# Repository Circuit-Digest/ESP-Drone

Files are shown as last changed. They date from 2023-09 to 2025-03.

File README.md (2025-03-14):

# ESP-Drone

image_tooltip
<br>

<br>

For a full tutorial check out our [ESP32 Drone Article](https://circuitdigest.com/microcontroller-projects/DIY-wifi-controlled-drone).
For working video:  [How to build an ESP32 Drone](https://youtu.be/uzZjk0TQKtU).

Drones have rapidly evolved from niche hobbies to versatile tools with a wide range of applications, from photography to agriculture or even for defense and military purposes. Depending on the application, features and payload capacity their price will vary from pocket changes to a few million. Even though the basic principle behind these drones may appear simple, there is a lot of technology and computation that goes behind it for proper operations and a desired result from these drones. For example, maintaining stability while in the air requires precision sensors such as a Gyroscope and proper processing of reading taken with it. In this project we are going to make such a drone which can be easily controlled using our phones.
This DIY drone is small in size and can be built using easily available components such as ESP32 modules, MPU6050 IMU, coreless motors and plastic propellers.

<br>**For anyone who is trying to flash the firmware using ESP32 Flash Download Tool, here are the file offsets for each binary**
<br>**0x1000 bootloader.bin**
<br>**0x8000 partition-table.bin**
<br>**0x10000 ESPDrone.bin**
<br>
[Note: As this projects are very simple we are only providing the code, schemaitic, and a few essential images if you want to get the images or code explanations do check out the Circuit Digest website.
<br>
<br>

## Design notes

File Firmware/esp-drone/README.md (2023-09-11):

## ESP-Drone

* [中文](./README_cn.md)

### Introduction

**ESP-Drone** is an open source solution based on Espressif ESP32/ESP32-S2/ESP32-S3 Wi-Fi chip, which can be controlled by a mobile APP or gamepad over **Wi-Fi** connection. ESP-Drone comes with **simple hardware**, **clear and extensible code architecture**, and therefore this project can be used in **STEAM education** and other fields. The main code is ported from **Crazyflie** open source project with **GPL3.0** protocol.

> Currently support ESP32、ESP32S2、ESP32S3, please using ESP-IDF [release/v4.4](https://docs.espressif.com/projects/esp-idf/en/release-v4.4/esp32s2/get-started/index.html) branch as your develop environment

ESP-Drone

For more information, please check the sections below:
* **Getting Started**: [Getting Started](https://docs.espressif.com/projects/espressif-esp-drone/zh_CN/latest/gettingstarted.html)
* **Hardware Schematic**：[Hardware](https://docs.espressif.com/projects/espressif-esp-drone/zh_CN/latest/_static/ESP32_S2_Drone_V1_2/SCH_Mainboard_ESP32_S2_Drone_V1_2.pdf)
* **iOS APP Source code**: [ESP-Drone-iOS](https://github.com/EspressifApps/ESP-Drone-iOS)
* **Android APP Source code**: [ESP-Drone-Android](https://github.com/EspressifApps/ESP-Drone-Android)

### Features

1. Stabilize Mode
2. Height-hold Mode
3. Position-hold Mode
4. APP Control
5. CFclient Supported

Note: to implement Height-hold/Position-hold mode, extension boards are needed. For more information, see Hardware Reference. 

### Third Party Copyrighted Code

Additional third party copyrighted code is included under the following licenses.

| Component | License | Origin |Commit ID |
| :---:  | :---: | :---: |:---: |
| core/crazyflie | GPL3.0  |[Crazyflie](https://github.com/bitcraze/crazyflie-firmware) |tag_2021_01 b448553|
| lib/dsp_lib |  | [esp32-lin](https://github.com/whyengineer/esp32-lin/tree/master/components/dsp_lib) |6fa39f4c|

### Support Policy

From December 2022, we will offer limited support on this project, but Pull Request is still welcomed!

### THANKS

1. Thanks to Bitcraze for the great [Crazyflie project](https://www.bitcraze.io/%20).
2. Thanks to Espressif for the powerful [ESP-IDF framework](https://docs.espressif.com/projects/esp-idf/en/latest/esp32s2/get-started/index.html).
3. Thanks to WhyEngineer for the useful [ESP-DSP lib](https://github.com/whyengineer/esp32-lin/tree/master/components/dsp_lib).

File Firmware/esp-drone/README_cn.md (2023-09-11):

## ESP-Drone

* [English Version](./README.md)

### 简介

ESP-Drone 是基于乐鑫 ESP32/ESP32-S2/ESP32-S3 开发的小型无人机解决方案，可使用手机 APP 或游戏手柄通过 Wi-Fi 网络进行连接和控制。目前已支持自稳定飞行、定高飞行、定点飞行等多种模式。该方案硬件结构简单，代码架构清晰完善，方便功能扩展，可用于 STEAM 教育等领域。控制系统代码来自 Crazyflie 开源工程，使用 GPL3.0 开源协议。

> 目前已支持 ESP32、ESP32S2、ESP32S3, 请使用 ESP-IDF [release/v4.4](https://docs.espressif.com/projects/esp-idf/en/release-v4.4/esp32s2/get-started/index.html) 分支

ESP-Drone

* **从这里开始**: [Getting Started](https://docs.espressif.com/projects/espressif-esp-drone/zh_CN/latest/gettingstarted.html)
* **硬件原理图**：[Hardware](https://docs.espressif.com/projects/espressif-esp-drone/zh_CN/latest/_static/ESP32_S2_Drone_V1_2/SCH_Mainboard_ESP32_S2_Drone_V1_2.pdf)
* **iOS APP 源代码**: [ESP-Drone-iOS](https://github.com/EspressifApps/ESP-Drone-iOS)
* **Android APP 源代码**: [ESP-Drone-Android](https://github.com/EspressifApps/ESP-Drone-Android)

### 功能

1. 自稳定模式
2. 定高模式
3. 定点模式
4. APP 控制
5. 适配 cfclient 上位机 

注意，定高模式及定点模式需外接扩展板，详情见硬件参考。

### 支持政策

自 2022 年 12 月起，我们仅提供有限的支持，但是 Pull Request 仍然是被欢迎的！

### 第三方代码

第三方代码及证书如下：

| 组件 | License | 源代码 |Commit ID |
| :---:  | :---: | :---: |:---: |
| core/crazyflie | GPL-3.0 |[Crazyflie](https://github.com/bitcraze/crazyflie-firmware) |tag_2021_01 b448553|
| lib/dsp_lib |  | [esp32-lin](https://github.com/whyengineer/esp32-lin/tree/master/components/dsp_lib) |6fa39f4c|

### 致谢

1. 感谢 Bitcraze 开源组织提供很棒的 [Crazyflie](https://www.bitcraze.io/%20) 无人机项目代码；
2. 感谢乐鑫提供 ESP32 和 [ESP-IDF 操作系统](https://docs.espressif.com/projects/esp-idf/en/latest/esp32s2/get-started/index.html)；
3. 感谢 WhyEngineer 提供的 stm32 dsp 移植库 [esp-dsp](https://github.com/whyengineer/esp32-lin/tree/master/components/dsp_lib)。

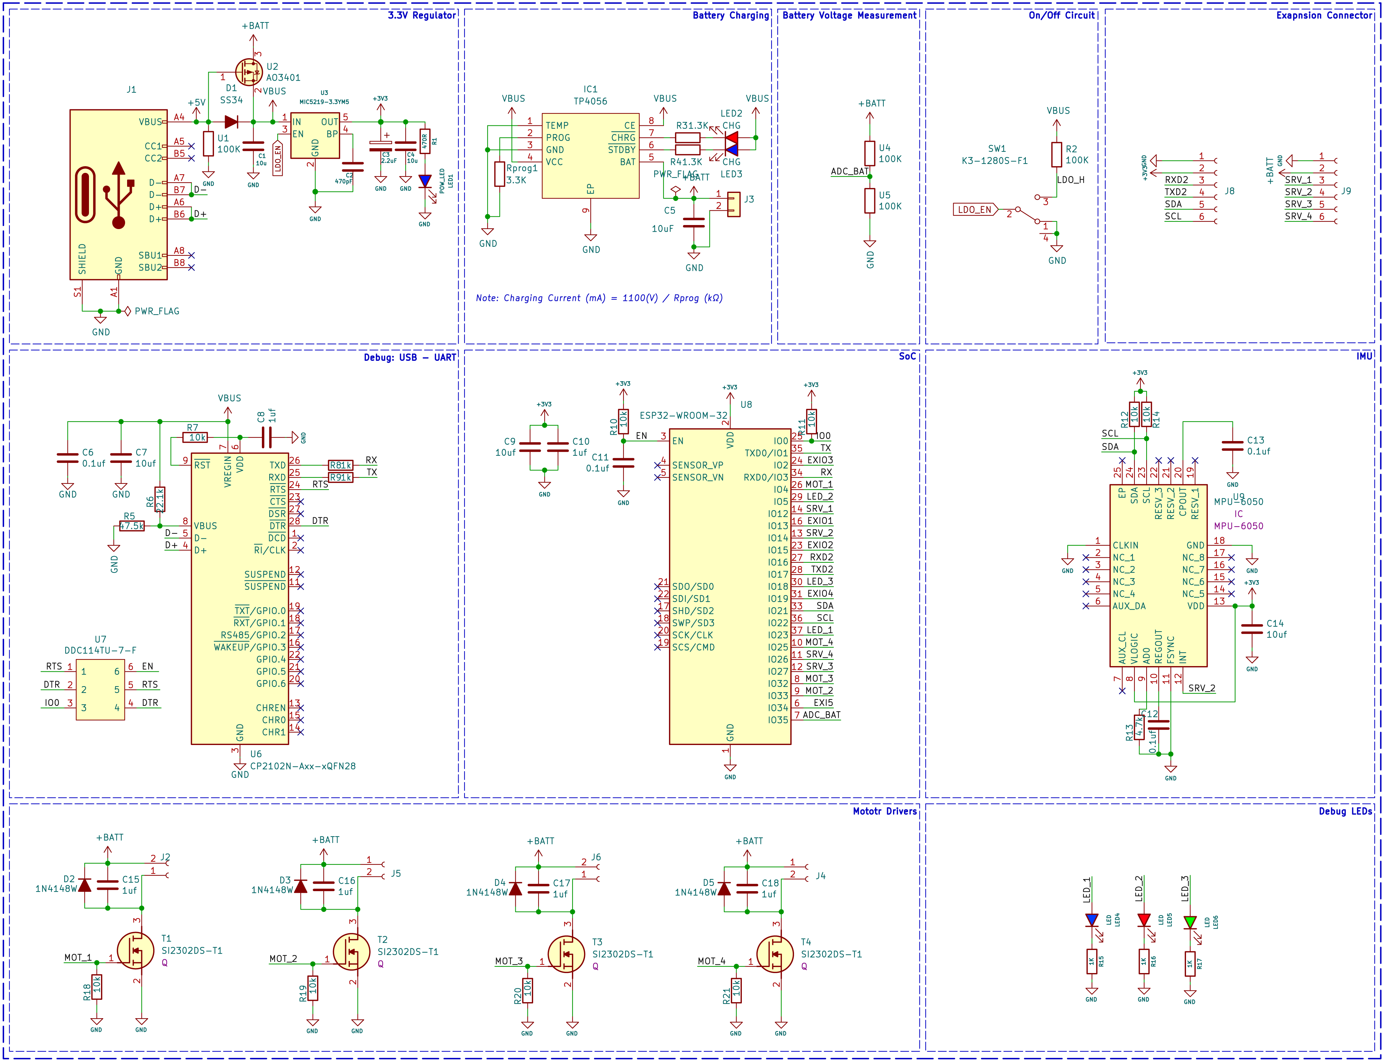
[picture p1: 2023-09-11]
ESP32 drone Schematics.png

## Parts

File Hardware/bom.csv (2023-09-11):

Designator | Footprint | Quantity | Value | LCSC Part #
C1, C4 | 603 | 2 | 10u
C10, C15, C16, C17, C18, C8 | 603 | 6 | 1uf
C11, C12, C13, C6 | 603 | 4 | 0.1uf
C14, C5, C7, C9 | 603 | 4 | 10uf
C2 | 603 | 1 | 470pF
C3 | 805 | 1 | 2.2uF
D1 | D_SMA | 1 | SS34
D2, D3, D4, D5 | D_SOD-323 | 4 | 1N4148W
IC1 | SOIC127P600X175-9N | 1 | TP4056
J1 | USB_C_Receptacle_HRO_TYPE-C-31-M-12 | 1 | USB_C_Receptacle_USB2.0
J2, J4, J5, J6 | JST_GH_SM02B-GHS-TB_1x02-1MP_P1.25mm_Horizontal | 4 | Conn_01x02_Female
J3 | JST_PH_B2B-PH-SM4-TB_1x02-1MP_P2.00mm_Vertical | 1 | B2B-PH-SM4-TB(LF)(SN)
J8, J9 | PinHeader_1x06_P2.54mm_Vertical | 2 | Conn_01x06_Female
LED1 | 603 | 1 | POW_LED
LED2, LED3 | 603 | 2 | CHG
LED4, LED5, LED6 | 603 | 3 | LED
R1 | 603 | 1 | 470R
R10, R11, R12, R14, R18, R19, R20, R21, R7 | 603 | 9 | 10k
R13 | 603 | 1 | 4.7k
R15, R16, R17, R8, R9 | 603 | 5 | 1K
R2, U1, U4, U5 | 603 | 4 | 100K
R3, R4 | 603 | 2 | 1.3K
R5 | 603 | 1 | 47.5k
R6 | 603 | 1 | 22.1k
Rprog1 | 603 | 1 | 3.3K
SW1 | slide switch spdt | 1 | K3-1280S-F1
T1, T2, T3, T4 | SOT95P237X112-3N | 4 | SI2302DS-T1
U2 | SOT-23 | 1 | AO3401
U3 | SOT-23-5 | 1 | MIC5219-3.3YM5
U6 | QFN-28-1EP_5x5mm_P0.5mm_EP3.35x3.35mm | 1 | CP2102N-Axx-xQFN28
U7 | SOT-363_SC-70-6 | 1 | 2N7002D
U8 | ESP32-WROOM-32 | 1 | ESP32-WROOM-32
U9 | MPU6050 | 1 | MPU-6050

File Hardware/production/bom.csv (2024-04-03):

Designator | Footprint | Quantity | Value | LCSC Part #
C1, C4 | 0603 | 2 | 10u
C10, C15, C16, C17, C18, C8 | 0603 | 6 | 1uf
C11, C12, C13, C6 | 0603 | 4 | 0.1uf
C14, C5, C7, C9 | 0603 | 4 | 10uf
C2 | 0603 | 1 | 470pF
C3 | 0805 | 1 | 2.2uF
D1 | D_SMA | 1 | SS34
D2, D3, D4, D5 | D_SOD-323 | 4 | 1N4148W
IC1 | SOIC127P600X175-9N | 1 | TP4056
J1 | USB_C_Receptacle_HRO_TYPE-C-31-M-12 | 1 | USB_C_Receptacle_USB2.0
J2, J4, J5, J6 | JST_GH_SM02B-GHS-TB_1x02-1MP_P1.25mm_Horizontal | 4 | Conn_01x02_Female
J3 | JST_PH_B2B-PH-SM4-TB_1x02-1MP_P2.00mm_Vertical | 1 | B2B-PH-SM4-TB(LF)(SN)
J8, J9 | PinHeader_1x06_P2.54mm_Vertical | 2 | Conn_01x06_Female
LED1 | 0603 | 1 | POW_LED
LED2, LED3 | 0603 | 2 | CHG
LED4, LED5, LED6 | 0603 | 3 | LED
R1 | 0603 | 1 | 470R
R10, R11, R12, R14, R18, R19, R20, R21, R7 | 0603 | 9 | 10k
R13 | 0603 | 1 | 4.7k
R15, R16, R17, R8, R9 | 0603 | 5 | 1K
R2, U1, U4, U5 | 0603 | 4 | 100K
R3, R4 | 0603 | 2 | 1.3K
R5 | 0603 | 1 | 47.5k
R6 | 0603 | 1 | 22.1k
Rprog1 | 0603 | 1 | 3.3K
SW1 | slide switch spdt | 1 | K3-1280S-F1
T1, T2, T3, T4 | SOT95P237X112-3N | 4 | SI2302DS-T1
U2 | SOT-23 | 1 | AO3401
U3 | SOT-23-5 | 1 | MIC5219-3.3YM5
U6 | QFN-28-1EP_5x5mm_P0.5mm_EP3.35x3.35mm | 1 | CP2102N-Axx-xQFN28
U7 | SOT-363_SC-70-6 | 1 | 2N7002DW
U8 | ESP32-WROOM-32 | 1 | ESP32-WROOM-32
U9 | MPU6050 | 1 | MPU-6050

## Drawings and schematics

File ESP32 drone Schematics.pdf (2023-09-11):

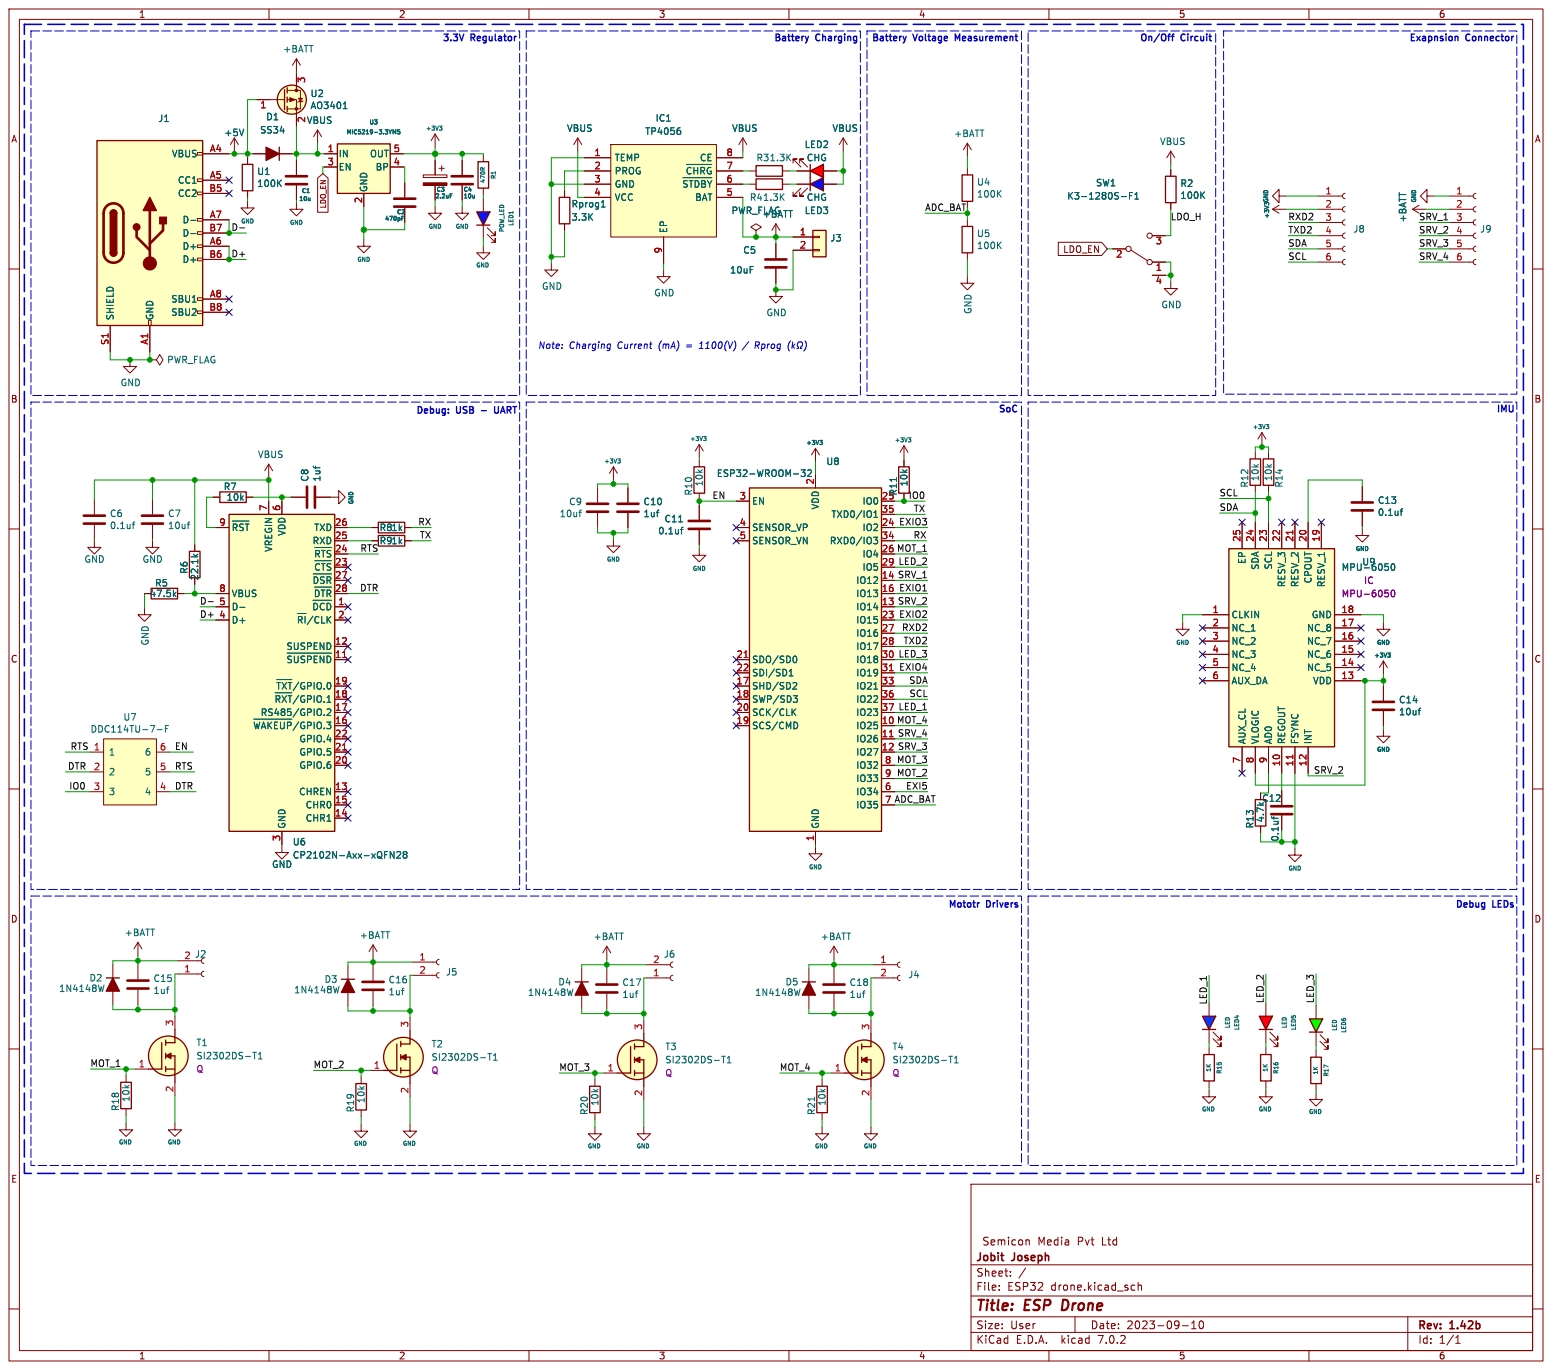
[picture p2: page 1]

IMU On/Off Circuit C8 1uf R7

Battery Voltage Measurement Note: Charging Current (mA) = 1100(V) / Rprog þÿ(k©) 3.3V Regulator

2 EN 3 BP 4 OUT 5 VBUS VBUS Rprog1

3.3K U6 CP2102N-Axx-xQFN28 ~{DCD}1 ~{SUSPEND}11 SUSPEND 12 CHREN 13 CHR1 14 CHR0 15 ~{WAKEUP}/GPIO.3

2 GPIO.6 20 GPIO.5 21 GPIO.4 22 ~{CTS} 23 ~{RTS} 24 RXD 25 TXD 26 ~{DSR} 27 ~{DTR} 28 GND

7 VBUS 8 ~{RST} 9 GND GND

~{DCD}1 ~{SUSPEND}11 SUSPEND 12 CHREN 13 CHR1 14 CHR0 15 ~{WAKEUP}/GPIO.3

2 SCK/CLK 20 SDO/SD0 21 SDI/SD1 22

Id: 1/1 Title: ESP Drone

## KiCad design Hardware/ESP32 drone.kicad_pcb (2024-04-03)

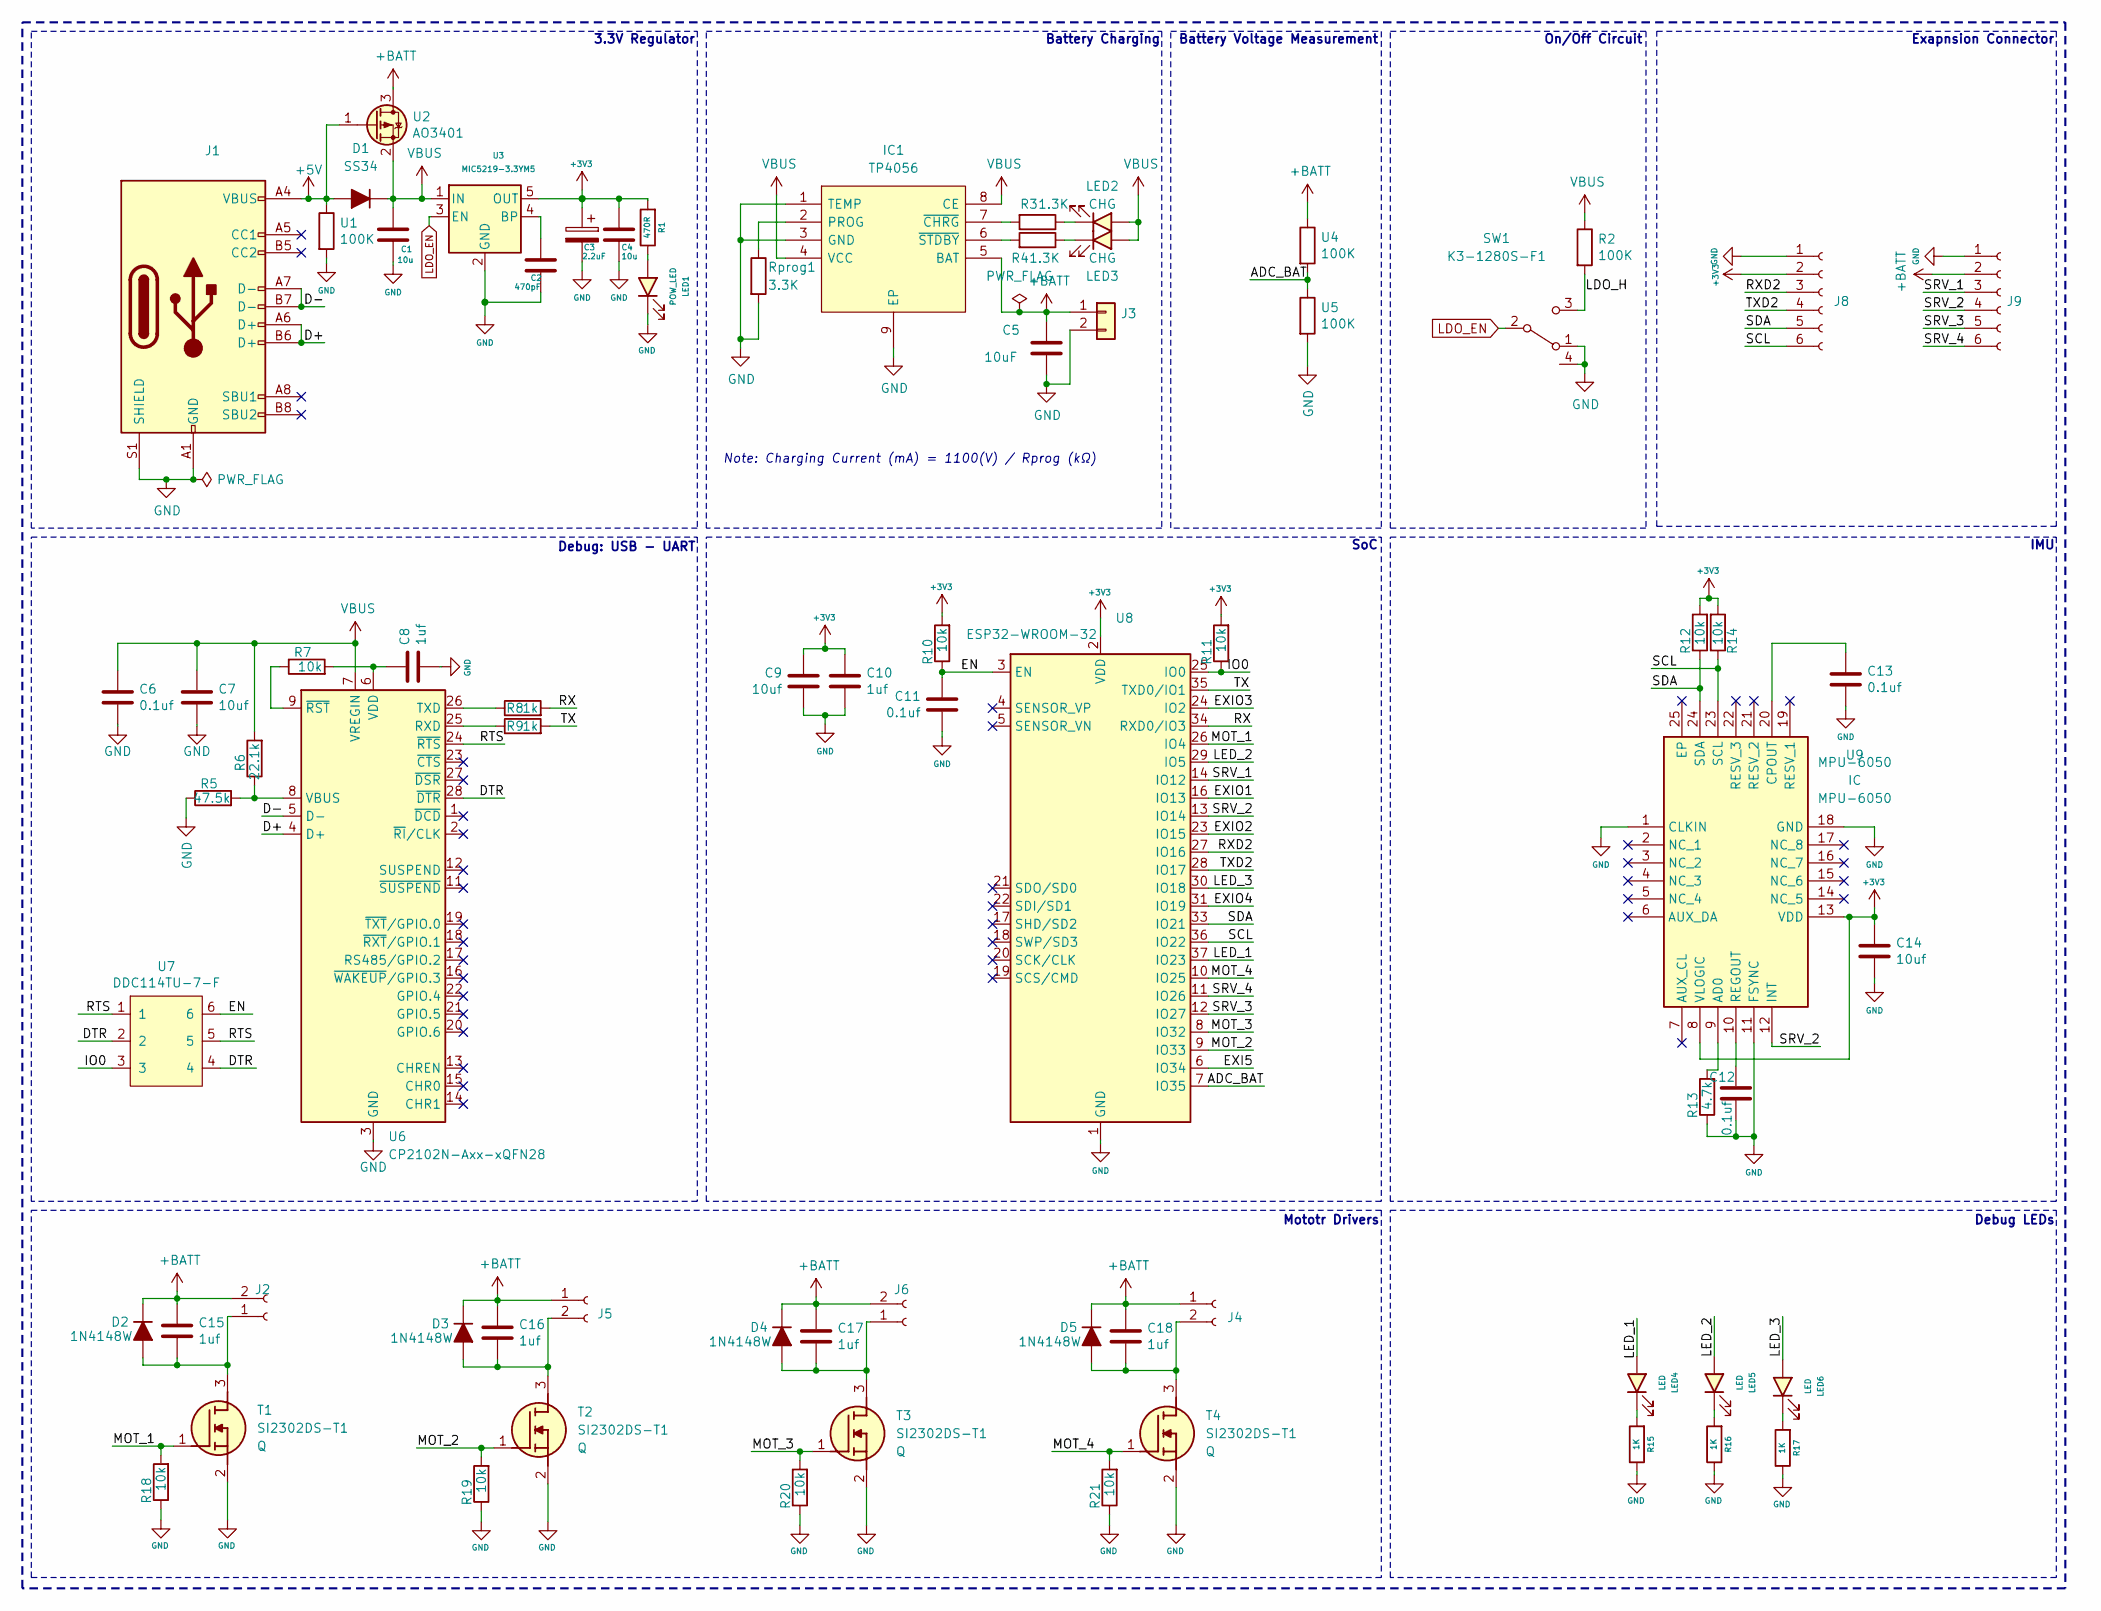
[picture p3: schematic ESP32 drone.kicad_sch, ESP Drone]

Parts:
C1, C4: 10u; C_0603_1608Metric
C2: 470pF; C_0603_1608Metric
C3: 2.2uF; C_0805_2012Metric
C5: 10uF; C_0603_1608Metric
C6, C11, C12, C13: 0.1uf; C_0603_1608Metric
C7, C9, C14: 10uf; C_0603_1608Metric
C8, C10, C15, C16, C17, C18: 1uf; C_0603_1608Metric
D1: SS34; D_SMA
D2, D3, D4, D5: 1N4148W; D_SOD-323
IC1: TP4056; SOIC127P600X175-9N; Manufacturer_Part_Number TP4056-42-ESOP8
J1: USB_C_Receptacle_USB2.0; USB_C_Receptacle_HRO_TYPE-C-31-M-12
J2, J4, J5, J6: Conn_01x02_Female; JST_GH_SM02B-GHS-TB_1x02-1MP_P1.25mm_Horizontal
J3: B2B-PH-SM4-TB(LF)(SN); JST_PH_B2B-PH-SM4-TB_1x02-1MP_P2.00mm_Vertical
J8, J9: Conn_01x06_Female; PinHeader_1x06_P2.54mm_Vertical
LED1: POW_LED; LED_0603_1608Metric
LED2, LED3: CHG; LED_0603_1608Metric
LED4, LED5, LED6: LED; LED_0603_1608Metric
R1: 470R; R_0603_1608Metric
R2: 100K; R_0603_1608Metric
R3, R4: 1.3K; R_0603_1608Metric
R5: 47.5k; R_0603_1608Metric
R6: 22.1k; R_0603_1608Metric
R7, R10, R11, R12, R14, R18, R19, R20, R21: 10k; R_0603_1608Metric
R8, R9: 1k; R_0603_1608Metric
R13: 4.7k; R_0603_1608Metric
R15, R16, R17: 1K; R_0603_1608Metric
Rprog1: 3.3K; R_0603_1608Metric
SW1: K3-1280S-F1; slide switch spdt
T1, T2, T3, T4: SI2302DS-T1; SOT95P237X112-3N; Mouser Part Number 781-SI2302DS
U1, U4, U5: 100K; R_0603_1608Metric
U2: AO3401; SOT-23
U3: MIC5219-3.3YM5; SOT-23-5
U6: CP2102N-Axx-xQFN28; QFN-28-1EP_5x5mm_P0.5mm_EP3.35x3.35mm
U7: DDC114TU-7-F; SOT-363_SC-70-6
U8: ESP32-WROOM-32
U9: MPU-6050; MPU6050; Mouser Part Number 410-MPU-6050

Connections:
+3V3: C3.1, C4.1, C9.1, C10.1, C14.1, J8.2, R1.2, R10.2, R11.2, R12.2, R14.2, U3.5 (OUT), U8.2 (VDD), U9.8 (VLOGIC), U9.13 (VDD)
+5V: D1.2 (A), J1.A4 (VBUS), J1.A9 (VBUS), J1.B4 (VBUS), J1.B9 (VBUS), U1.1, U2.1 (G)
+BATT: C5.1, C15.1, C16.1, C17.1, C18.1, D2.1 (K), D3.1 (K), D4.1 (K), D5.1 (K), IC1.5 (BAT), J2.2, J3.1, J4.1, J5.1, J6.2, J9.2, U2.3 (D), U4.1
/ADC_BAT: U4.2, U5.1, U8.7 (IO35)
/D+: J1.A6 (D+), J1.B6 (D+), U6.4 (D+)
/D-: J1.A7 (D-), J1.B7 (D-), U6.5 (D-)
/DTR: U6.28 (~DTR), U7.2, U7.4
/EN: C11.1, R10.1, U7.6, U8.3 (EN)
/EXI5: U8.6 (IO34)
/EXIO1: U8.16 (IO13)
/EXIO2: U8.23 (IO15)
/EXIO3: U8.24 (IO2)
/EXIO4: U8.31 (IO19)
/IO0: R11.1, U7.3, U8.25 (IO0)
/LDO_H: R2.2, SW1.3 (C)
/LED_1: LED4.2 (A), U8.37 (IO23)
/LED_2: LED5.2 (A), U8.29 (IO5)
/LED_3: LED6.2 (A), U8.30 (IO18)
/MOT_1: R18.2, T1.1 (G), U8.26 (IO4)
/MOT_2: R19.2, T2.1 (G), U8.9 (IO33)
/MOT_3: R20.2, T3.1 (G), U8.8 (IO32)
/MOT_4: R21.2, T4.1 (G), U8.10 (IO25)
/RTS: U6.24 (~RTS), U7.1, U7.5
/RX: R8.2, U8.34 (RXD0/IO3)
/RXD2: J8.3, U8.27 (IO16)
/SCL: J8.6, R14.1, U8.36 (IO22), U9.23 (SCL)
/SDA: J8.5, R12.1, U8.33 (IO21), U9.24 (SDA)
/SRV_1: J9.3, U8.14 (IO12)
/SRV_2: J9.4, U8.13 (IO14), U9.12 (INT)
/SRV_3: J9.5, U8.12 (IO27)
/SRV_4: J9.6, U8.11 (IO26)
/TX: R9.2, U8.35 (TXD0/IO1)
/TXD2: J8.4, U8.28 (IO17)
GND: C1.2, C2.2, C3.2, C4.2, C5.2, C6.2, C7.2, C8.2, C9.2, C10.2, C11.2, C12.2, C13.2, C14.2, IC1.1 (TEMP), IC1.3 (GND), IC1.9 (EP), J1.A1 (GND), J1.A12 (GND), J1.B1 (GND), J1.B12 (GND), J1.S1 (SHIELD), J3.2, J8.1, J9.1, LED1.1 (K), R5.1, R13.1, R15.1, R16.1, R17.1, R18.1, R19.1, R20.1, R21.1, Rprog1.2, SW1.1 (A), SW1.4, T1.2 (S), T2.2 (S), T3.2 (S), T4.2 (S), U1.2, U3.2 (GND), U5.2, U6.3 (GND), U6.29 (GND), U8.1 (GND), U8.15 (GND), U8.38 (GND), U8.39 (GND), U9.1 (CLKIN), U9.11 (FSYNC), U9.18 (GND)
LDO_EN: SW1.2 (B), U3.3 (EN)
unnamed: C15.2, D2.2 (A), J2.1, T1.3 (D)
unnamed: C16.2, D3.2 (A), J5.2, T2.3 (D)
unnamed: C17.2, D4.2 (A), J6.1, T3.3 (D)
unnamed: C18.2, D5.2 (A), J4.2, T4.3 (D)
unnamed: IC1.2 (PROG), Rprog1.1
unnamed: IC1.7 (~CHRG), R3.2
unnamed: IC1.6 (~STDBY), R4.2
unnamed: LED1.2 (A), R1.1
unnamed: LED2.1 (K), R3.1
unnamed: LED3.1 (K), R4.1
unnamed: LED4.1 (K), R15.2
unnamed: LED5.1 (K), R16.2
unnamed: LED6.1 (K), R17.2
unnamed: C2.1, U3.4 (BP)
unnamed: R9.1, U6.25 (RXD)
unnamed: R8.1, U6.26 (TXD)
unnamed: R5.2, R6.1, U6.8 (VBUS)
unnamed: C8.1, R7.2, U6.6 (VDD)
unnamed: R7.1, U6.9 (~RST)
unnamed: R13.2, U9.9 (AD0)
unnamed: C13.1, U9.20 (CPOUT)
unnamed: C12.1, U9.10 (REGOUT)
VBUS: C1.1, C6.1, C7.1, D1.1 (K), IC1.4 (VCC), IC1.8 (CE), LED2.2 (A), LED3.2 (A), R2.1, R6.2, U2.2 (S), U3.1 (IN), U6.7 (VREGIN)

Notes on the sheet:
SoC
Battery Voltage Measurement
IMU
Mototr Drivers
Battery Charging
Debug LEDs
Debug: USB - UART
Exapnsion Connector
3.3V Regulator
Note: Charging Current (mA) = 1100(V) / Rprog (kΩ)
On/Off Circuit

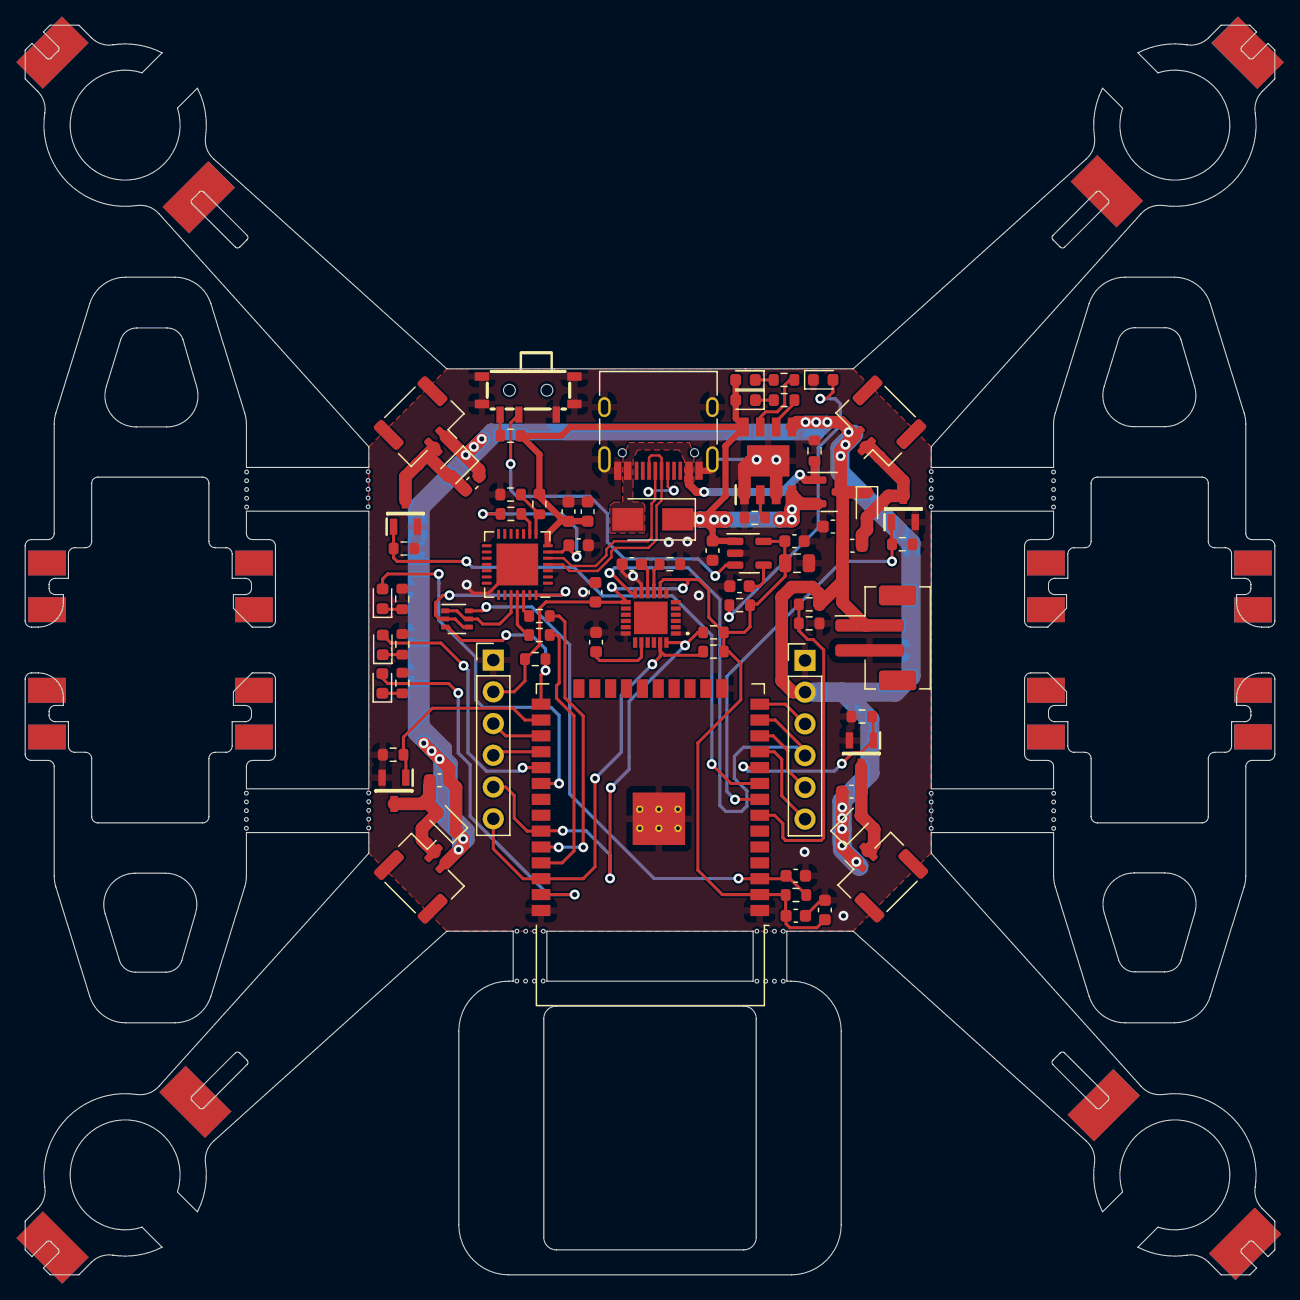
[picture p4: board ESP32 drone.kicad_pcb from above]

Board: 2 copper layers, 100.0 x 100.0 mm, 74 parts (0 on the bottom side), 53 nets.

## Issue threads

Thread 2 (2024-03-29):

Dimension marking is in EdgeCut Layer !

draj1234, 2024-03-29:
Hi your work is super ! but in Gerber the 100mm dimension markings is put in Edgecut layer ! Because of that when we upload the gerber to PCB house software it shows up some odd shape ! Can you help to release by moving that dimension marking to other layers and re-release the Gerber !
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

draj1234, 2024-03-29:
This is what shows up in  a PCB house's Gerber viewer - Not sure how the PCB house will take it up or Reject it , Please review and help to release the corrected Gerber - Or help by letting know the community know how to handle it when PCB ordering.  Anyway Thanks for your efforts.
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

omalave, 2024-04-05:
I had not issues with PCB when I sent to pcbway.com
Use my ref link if you want.
https://pcbway.com/g/OW8F6X

draj1234, 2024-04-13:
Hi Omalave, Thankyou for your response, but somehow when I click the link you had given it lands up to the pcbway.com's standard home page rather then any reference link, can you help to look at it.

jeffhuys, 2024-09-19:
> Hi Omalave, Thankyou for your response, but somehow when I click the link you had given it lands up to the pcbway.com's standard home page rather then any reference link, can you help to look at it.

That's because it's a referral link. If you click on it and buy something, @omalave gets commision. The link will not help you.

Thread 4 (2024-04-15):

USB-C PD Issue

petrkr, 2024-04-15:
You do not have connected CC1 and CC2 on USB-C connector, so USB-C chargers will NOT work. Only legacy USB-A-->USB-C cables will work.
Dont worry, similar issue had Raspberry Pi 4B on first release.

Make it like this, tested on our ESP32C3 board
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

Btw nice project, regards Petr

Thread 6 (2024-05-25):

how to use different modes position control

NBL-NZ, 2024-05-25:
i have connected pressure sensor module. how to use different modes in   drone mentioned in the  features.  does aopplication have any particular setting to enable it?

saaraswata, 2024-08-01:
Hey I have the same issue, any way to do it?

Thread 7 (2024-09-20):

code cannot be flashed/uploaded

qurrpurr, 2024-09-20:
I am new to using esp-idf so i may not not know a lot but this error occurs when i tried to build it.

`CMake Error at run_serial_tool.cmake:56 (message):
  C:/Espressif/python_env/idf4.4_py3.8_env/Scripts/python.exe
  C:/Espressif/frameworks/esp-idf-v4.4/components/esptool_py/esptool/esptool.py
  --chip esp32 failed

FAILED: CMakeFiles/flash
cmd.exe /C "cd /D C:\Espressif\frameworks\esp-idf-v4.4\components\esptool_py && C:\Espressif\tools\cmake\3.20.3\bin\cmake.exe -D IDF_PATH="C:/Espressif/frameworks/esp-idf-v4.4" -D SERIAL_TOOL="C:/Espressif/python_env/idf4.4_py3.8_env/Scripts/python.exe C:/Espressif/frameworks/esp-idf-v4.4/components/esptool_py/esptool/esptool.py --chip esp32" -D SERIAL_TOOL_ARGS="--before=default_reset --after=hard_reset write_flash @flash_args" -D WORKING_DIRECTORY="C:/Espressif/frameworks/esp-idf-v4.4/ESP-Drone/Firmware/esp-drone/build" -P C:/Espressif/frameworks/esp-idf-v4.4/components/esptool_py/run_serial_tool.cmake"
ninja: build stopped: subcommand failed.
ninja failed with exit code 1`

IDF Version: v4.4.
SoC Chip:
Hardware: ESP32_S2_Drone_V1_2

qurrpurr, 2024-09-21:
turns out i just need to chose the board lol

dush123kumar, 2024-09-24:
I can give an answer but it's not useful for me by answering it .....

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

Closed 2024-09-21.

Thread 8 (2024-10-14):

2n7002D vs DDC114TU-7-f

marcus-4, 2024-10-14:
Hi, The BOM contains an entry U7 IC for the 2n7002D dual MOSFET SOT363 package, but the schematic calls for the DDC114TU dual BJT device in this package. I noticed the original Espressif design uses the BC847BDW1T1G SOT363 dual BJT device, which seems closer to the U7 in the schematic, not the BOM. I was wondering if this discrepancy is a mistake, and which chip should be used?

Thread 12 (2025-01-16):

Kalman estimator does not work after flowdeck v2 integration

saikrishnarao2, 2025-01-16:
I tried to fly with the app. Immediately after the connect, motors starts spinning randomly, unable to take off.

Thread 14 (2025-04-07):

kicad pcb file is not showing properly

Kalki2898add, 2025-04-07:
i am tring to edit your pcb . i imported the pcb file to kicad 9 but some green lines appears.

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
 and i also tried other pcb editor like easyeda that also not showing the pcb properly

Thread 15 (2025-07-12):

MPU6050 Connection Fail

praveens-git, 2025-07-12:
Hi, I have tried to run this code on my board, but I am getting

```
I (1312) EEPROM: spi_flash_init ... !
I (1312) EEPROM: spi_flash_read ok !
Characterized using eFuse Vref
I (3574) I2CDRV:  i2c 0 driver install return = 0
E (3591) SENSORS: MPU6050 I2C connection [FAIL].

```

I have checked MPU6050 using a simple arduino script, and it works fine

Anybody has solution to this?

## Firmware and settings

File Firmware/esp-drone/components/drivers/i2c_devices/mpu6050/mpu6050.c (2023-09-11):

// I2Cdev library collection - MPU6050 I2C device class
// Based on InvenSense MPU-6050 register map document rev. 2.0, 5/19/2011 (RM-MPU-6000A-00)
// 8/24/2011 by Jeff Rowberg <jeff@rowberg.net>
// Updates should (hopefully) always be available at https://github.com/jrowberg/i2cdevlib

/* ============================================
 I2Cdev device library code is placed under the MIT license
 Copyright (c) 2011 Jeff Rowberg
 Adapted to Crazyflie FW by Bitcraze

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
 THE SOFTWARE IS PROVIDED "AS IS", WITHOUT WARRANTY OF ANY KIND, EXPRESS OR
 IMPLIED, INCLUDING BUT NOT LIMITED TO THE WARRANTIES OF MERCHANTABILITY,
 FITNESS FOR A PARTICULAR PURPOSE AND NONINFRINGEMENT. IN NO EVENT SHALL THE
 AUTHORS OR COPYRIGHT HOLDERS BE LIABLE FOR ANY CLAIM, DAMAGES OR OTHER
 LIABILITY, WHETHER IN AN ACTION OF CONTRACT, TORT OR OTHERWISE, ARISING FROM,
 OUT OF OR IN CONNECTION WITH THE SOFTWARE OR THE USE OR OTHER DEALINGS IN
 THE SOFTWARE.
 ===============================================
 */

#include "freertos/FreeRTOS.h"
#include "freertos/task.h"

#include "i2cdev.h"
#include "mpu6050.h"
#include "eprintf.h"
#include "stm32_legacy.h"
#define DEBUG_MODULE "MPU6050"
#include "debug_cf.h"

static uint8_t devAddr;
static I2C_Dev *I2Cx;
static uint8_t buffer[14];
static bool isInit;

/** Default constructor, uses default I2C address.
 * @see MPU6050_DEFAULT_ADDRESS
 */
void mpu6050Init(I2C_Dev *i2cPort)
{
    if (isInit) {
        return;
    }

    I2Cx = i2cPort;
    devAddr = MPU6050_ADDRESS_AD0_LOW;
    isInit = true;

}

bool mpu6050Test(void)
{
    bool testStatus;

    if (!isInit) {
        return false;
    }

    testStatus = mpu6050TestConnection();

    return testStatus;
}

/** Verify the I2C connection.
 * Make sure the device is connected and responds as expected.
 * @return True if connection is valid, false otherwise
 */
bool mpu6050TestConnection()
{
    return mpu6050GetDeviceID() == 0b110100;
}

/** Do a MPU6050 self test.
 * @return True if self test passed, false otherwise
 */
bool mpu6050SelfTest()
{
    bool testStatus = true;
    int16_t axi16, ayi16, azi16;
    int16_t gxi16, gyi16, gzi16;
    float axf, ayf, azf;
    float gxf, gyf, gzf;
    float axfTst, ayfTst, azfTst;
    float gxfTst, gyfTst, gzfTst;
    float axfDiff, ayfDiff, azfDiff;
    float gxfDiff, gyfDiff, gzfDiff;
    float gRange, aRange;
    uint32_t scrap;

    aRange = mpu6050GetFullScaleAccelGPL();
    gRange = mpu6050GetFullScaleGyroDPL();

    // First values after startup can be read as zero. Scrap a couple to be sure.
    for (scrap = 0; scrap < 5; scrap++) {
        mpu6050GetMotion6(&axi16, &ayi16, &azi16, &gxi16, &gyi16, &gzi16);
        vTaskDelay(M2T(2));
    }

    // First measurement
    gxf = gxi16 * gRange;
    gyf = gyi16 * gRange;
    gzf = gzi16 * gRange;
    axf = axi16 * aRange;
    ayf = ayi16 * aRange;
    azf = azi16 * aRange;

    // Enable self test
    mpu6050SetGyroXSelfTest(true);
    mpu6050SetGyroYSelfTest(true);
    mpu6050SetGyroZSelfTest(true);
    mpu6050SetAccelXSelfTest(true);
    mpu6050SetAccelYSelfTest(true);
    mpu6050SetAccelZSelfTest(true);

    // Wait for self test to take effect
    vTaskDelay(1000 / portTICK_PERIOD_MS);//vTaskDelay(M2T(MPU6050_SELF_TEST_DELAY_MS));
    // Take second measurement
    mpu6050GetMotion6(&axi16, &ayi16, &azi16, &gxi16, &gyi16, &gzi16);
    gxfTst = gxi16 * gRange;
    gyfTst = gyi16 * gRange;
    gzfTst = gzi16 * gRange;
    axfTst = axi16 * aRange;
    ayfTst = ayi16 * aRange;
    azfTst = azi16 * aRange;

    // Disable self test
    mpu6050SetGyroXSelfTest(false);
    mpu6050SetGyroYSelfTest(false);
    mpu6050SetGyroZSelfTest(false);
    mpu6050SetAccelXSelfTest(false);
    mpu6050SetAccelYSelfTest(false);
    mpu6050SetAccelZSelfTest(false);

// Read factory values
//  i2cdevReadByte(I2Cx, devAddr, 0x00, (uint8_t *)&gxfi8);
//  i2cdevReadByte(I2Cx, devAddr, 0x01, (uint8_t *)&gyfi8);
//  i2cdevReadByte(I2Cx, devAddr, 0x02, (uint8_t *)&gzfi8);
//  i2cdevReadByte(I2Cx, devAddr, 0x0D, (uint8_t *)&axfi8);
//  i2cdevReadByte(I2Cx, devAddr, 0x0E, (uint8_t *)&ayfi8);
//  i2cdevReadByte(I2Cx, devAddr, 0x0F, (uint8_t *)&azfi8);

//  fprintf("gxf:%i, gyf:%i, gzf:%i, axf:%i, ayf:%i, azf:%i\n",
//             (int)gxfi8, (int)gyfi8, (int)gzfi8, (int)axfi8, (int)ayfi8, (int)azfi8);

    // Calculate difference
    gxfDiff = gxfTst - gxf;
    gyfDiff = gyfTst - gyf;
    gzfDiff = gzfTst - gzf;
    axfDiff = axfTst - axf;
    ayfDiff = ayfTst - ayf;
    azfDiff = azfTst - azf;

    // Check result
    if (mpu6050EvaluateSelfTest(MPU6050_ST_GYRO_LOW, MPU6050_ST_GYRO_HIGH, gxfDiff, "gyro X") &&
            mpu6050EvaluateSelfTest(-MPU6050_ST_GYRO_HIGH, -MPU6050_ST_GYRO_LOW, gyfDiff, "gyro Y") &&
            mpu6050EvaluateSelfTest(MPU6050_ST_GYRO_LOW, MPU6050_ST_GYRO_HIGH, gzfDiff, "gyro Z") &&
            mpu6050EvaluateSelfTest(MPU6050_ST_ACCEL_LOW, MPU6050_ST_ACCEL_HIGH, axfDiff, "acc X") &&
            mpu6050EvaluateSelfTest(MPU6050_ST_ACCEL_LOW, MPU6050_ST_ACCEL_HIGH, ayfDiff, "acc Y") &&
            mpu6050EvaluateSelfTest(MPU6050_ST_ACCEL_LOW, MPU6050_ST_ACCEL_HIGH, azfDiff, "acc Z")) {
        DEBUG_PRINTD("mpu6050 Self test [OK].\n");
    } else {
        testStatus = false;
    }

    return testStatus;
}

/** Evaluate the values from a MPU6050 self test.
 * @param low The low limit of the self test
 * @param high The high limit of the self test
 * @param value The value to compare with.
 * @param string A pointer to a string describing the value.
 * @return True if self test within low - high limit, false otherwise
 */
bool mpu6050EvaluateSelfTest(float low, float high, float value, char *string)
{
    if (value < low || value > high) {
        DEBUG_PRINTD("Self test %s [FAIL]. low: %0.2f, high: %0.2f, measured: %0.2f\n",
                     string, (double)low, (double)high, (double)value);
        return false;
    }

    return true;
}

// AUX_VDDIO register (InvenSense demo code calls this RA_*G_OFFS_TC)

/** Get the auxiliary I2C supply voltage level.
 * When set to 1, the auxiliary I2C bus high logic level is VDD. When cleared to
 * 0, the auxiliary I2C bus high logic level is VLOGIC. This does not apply to
 * the MPU-6000, which does not have a VLOGIC pin.
 * @return I2C supply voltage level (0=VLOGIC, 1=VDD)
 */
uint8_t mpu6050GetAuxVDDIOLevel()
{
    i2cdevReadBit(I2Cx, devAddr, MPU6050_RA_YG_OFFS_TC, MPU6050_TC_PWR_MODE_BIT, buffer);
    return buffer[0];
}
/** Set the auxiliary I2C supply voltage level.
 * When set to 1, the auxiliary I2C bus high logic level is VDD. When cleared to
 * 0, the auxiliary I2C bus high logic level is VLOGIC. This does not apply to
 * the MPU-6000, which does not have a VLOGIC pin.
 * @param level I2C supply voltage level (0=VLOGIC, 1=VDD)
 */
void mpu6050SetAuxVDDIOLevel(uint8_t level)
{
    i2cdevWriteBit(I2Cx, devAddr, MPU6050_RA_YG_OFFS_TC, MPU6050_TC_PWR_MODE_BIT, level);
}

// SMPLRT_DIV register
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
